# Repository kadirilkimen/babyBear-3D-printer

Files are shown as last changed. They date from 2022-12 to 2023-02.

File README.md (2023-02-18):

# the babyBear 3D Printer
## A very small 3D printer! that slightly smaller than an A4 paper including a spool of filament.

Just the footprint is small. It has a 160mm diameter build plate and up to 300mm work height.
It's a complete 3D printer with quick change tool head. So the plan is making it a laser cutter and cnc milling machine along with printing.

```diff
+ All STL and BOM files have been updated.

! See the assembly animations on this link : https://kadirilkimen.com/babybear/assemblyanimations/
! Note that the animations are not final and not covers all the machine yet.
```
# Marlin now has Polar kinematics!
Finally, I developed polar kinematics and the Marlin team merged it to the main distribution.
That means you can just slice the model and send to the babyBear without post processing.

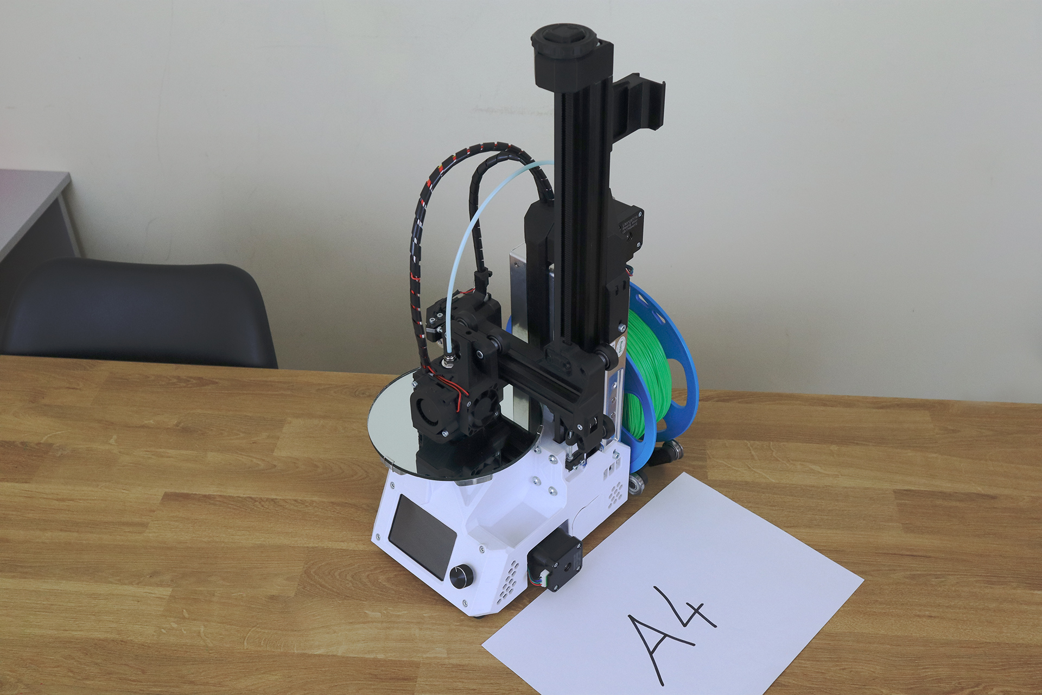
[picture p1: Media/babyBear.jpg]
babyBear Optional title


## Great people who helped me on this project.

Most of the babyBear components donated by V-slot Poland.

Filaments and some local logistics provided by RE3D filaments.

If you are located in Europe, I recommend you to visit their website.

https://vslot-poland.com/en_US/index

https://re3d.eu/

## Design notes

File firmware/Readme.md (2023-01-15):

# Intro
If you don't know how to work with firmware, jump to the **shortcut** section.
**babyBear_firmware.bin is a compiled Marlin to work with recommended controller board, display and drivers.**

### babyBear developed around and tested with Marlin firmware
It is possible to use a different firmware.
I just decided not to split my energy on a lot of options.
If you can make other firmware work with the babyBear, feel free to perform a pull request.

## shortcut
If you have the firmware file, it is very simple.
- download the firmware file [babyBear_firmware.bin](babyBear_firmware.bin).
- Put the firmware file into an SD card.
- Insert SD card into the machine.
- Turn on the machine.
- You would see messages like "erasing" or "uploading".
- Once it is done, you will see Marlin printer interface.
- Done! Happy printing!

## Basics
### If you don't need any customization and you have the recommended hardware
- Just follow the **shortcut** section.

### If you have different hardware or want to do some customizations with Marlin firmware
- Follow **How to install Marlin** and **How to configure Marlin**

### Ah, you are the rogue one?
- Well, at least take a look at configuration files here.

## How to install Marlin
Polar kinematics added to Marlin by bugfix.2.1.x

babyBear doesn't require any special step.
Please follow official Marlin guide:
https://marlinfw.org/docs/basics/install.html

Just like each machine, you must edit configuration.h and configuration_adv.h files
- If you are using the recommended hardware, you can use the [Configuration.h](Configuration.h) and [Configuration_adv.h](Configuration_adv.h) files.
- for other hardware, follow the **Configuration** section

## How to configure Marlin
- uncomment #define POLAR line.
- To have a starting point, copy the step, feedrate and acceleration settings from [Configuration.h](Configuration.h)
- uncomment #define LIN_ADVANCE line in the Configuration_adv.h file.
- Set ADVANCE_K to 0.15, or perform a calibration test to find out the best one. However,  polar axis motions near the center is weird and requires a lot of work. You would just save your time and go with 0.15 :)
- If you don't have the recommended hardware, perform the hardware related configurations. 

## Recommended and tested hardware
- MKS Robin nano v3 Board.
- TMC 2209 drivers
- MKS TS35 display.
- BMG type extruder with 3:1 reduction.

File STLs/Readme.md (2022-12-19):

# Read this before start printing

### Material
Original prototype printed with PETG filament.
Because it is an overall best compromise for;
- heat resistance,
- printability,
- dimensional stability,
- strength.

If you choose a different material, please keep in mind that electronics, motors and power supply creates significant heat.

### Part orientation
All parts are oriented according to required strength and printability.
I recommend printing all parts in their original orientation.

### Nozzle and layer height
Printable parts are designed to print with 0.4mm nozzle and 0.2mm layer height.
If you prefer less layer height, prefer 0.1mm. Other layer heights may cause some detail to be lost.

### Printing precise parts
Almost everything about FDM printing is relative and it is not simple to print precise parts.

#### Understanding temperature effects
Printing at a correct temperature is critical to achieve precision in FDM parts.
Filament manufacturers have their own material blends. Therefore, a very best temperature value for a filament wouldn't be the best for another brand.
The manufacturers mostly recommend best temperature range for their filaments.
Usually, printing at lower end of this range gives better surface quality, which is very important for precision.
However, lower temps. also reduces the fusing between layers and part becomes weaker.
So you would prefer to find best compromise spot between the surface quality and the strength.

#### Printer's positioning accuracy
Especially the 3D printers come as kits, mostly don't have a good positioning accuracy.
You would expect 0.1mm deviation on dimensions.
Parts of the babyBear designed to have 0.2mm tolerance to each other and off the shelf components.
Make sure your printer's positioning accuracy is better than 0.1mm.
If it is not, then calibrate your printer's hardware and stepper motors.

#### Squareness of the printer
Very less 3D printer model comes with a good square frame.
If your printer came as kit and you assembled it yourself, it is probably not square at all.
If you are into printing precision parts, I recommend you to get machinist right angle squares.

Using right angle, check all the linear rails and adjust them until they are square each other.
To get more information about squaring, it is called Tramming in machine industry. Check youtube for cnc machine/3d printer tramming.

Let's say if your printer is not square enough;
In this case Z axis wouldn't be parallel to the rotary axis of the babyBear. This means, in higher Z distances, your part will become narrower or wider.
Rotary axis rotor won't be cylinder enough and it will wobble. This wobble will be amplified by Z height.

So the squareness of your printer is very important.

#### Dimensional accuracy of the parts.
To make sure the 3D printed parts in a good tolerance, first print some test parts and try if they fit properly.

For example, I printed a section of rotary axis rotor to check 16010 bearing ID tolerance and again printed a section of the main body to check 16010 bearing OD tolerance.

Especially the bearings must fit to the place with a little tightness. If it is too tight, it will deform the printed body while mounting. If it is loose, it won't create precise movement under load.

On the bearing mounting surfaces, only use sanding to remove imperfections. If the surface is not accurate enough, then I recommend to print the part from scratch.

### Post processing
Even under best circumstances, 3D printed parts still can have problems.
FDM printers tend to smooth inside corners and make bulgy ends on outside corners.
So you have to sand down these imperfections, if necessary.

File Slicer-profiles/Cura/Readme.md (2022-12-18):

# Cura machine profile for the babyBear

## Instructions
- Go to the Cura configuration folder. You can find it in Cura main menu : Help > Show configuration folder.
- Make sure that there is no running Cura.
- Copy the "definition_changes", "machine_instances" and "user" folders into the configuration folder. Overwrite the folders.
- Next time you open Cura, you will see "the babyBear" next to your other printer profiles.

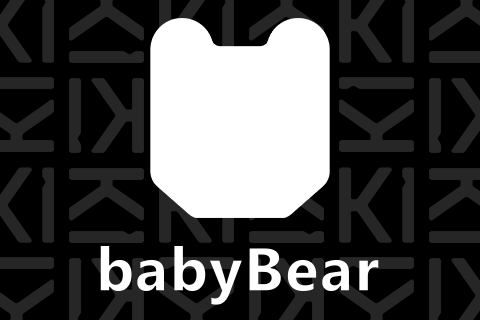
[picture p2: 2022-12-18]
Media/babyBear-bootscreen.png

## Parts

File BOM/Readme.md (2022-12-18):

## **ODS is a spreadsheet file format. Any office software can open it.**
### If you don't have office software, you can give Libreoffice a shot  https://www.libreoffice.org/

## **Components**
Component links are carefully selected. But I didn't buy them directly.
Most of the babyBear components donated by V-slot Poland.
The rest were collected from local stores.

I bought average quality 16010 bearings from a local store for 4USD each and F608 bearings from aliexpress for less than 1USD each.
I don't recommend cheapest bearings. They tend to be very bad. But best selling cheap bearings are usually good enough for such projects.

## **Consumables**
Consumable items you will need while building the babyBear.

## **Fasteners**
Online stores often sell fasteners in odd varieties and quantities.
It would be easier to get fasteners from a local shop.

There are different fastener grades. Usually you can see 8.8, 10.9, 12.9 etc.
Higher the number means stronger the fastener.
I recommend fasteners grade higher than 8.8 for this project.

## **Tools**
You probably will need those tools to build the babyBear.
They are also common tools for 3D printing and such projects.

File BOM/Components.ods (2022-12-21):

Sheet: Sheet1
Electronics
Type | Size | Quantity | Description | Amazon

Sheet: Sheet2
Electronics
Type | Size | Quantity | Description | Amazon
MKS Robin nano v3 controller +TS35 display + TMC2209 drivers | - | 1 | I recommend to buy them as a kit. | https://amzn.to/3um2EEK
24V – 350W Slim type Power supply. Dimensions are important! | W:115mm L:215mm H:30mm | 1 | Please keep in mind. Power quality affects overall electronics. I strictly recommend to use a good quality product | https://amzn.to/3h1wlbl
Stepper motor | Nema 17 | 4 | Min. 40mm length recommended. Connectors SH-2.54 | https://amzn.to/3VwYYfk
Snap fit – Power inlet (See reference photo. Any different power inlet won’t fit ) | - | 1 | Already wired one recommended to avoid working on AC current. | https://amzn.to/3HbvpvO
Limit switch (See reference photo) | 20mm | 2 | Any standard 3 pin microswitch would work. | https://amzn.to/3VwhR2a
Fan 24V | 40x40x10 | 2 | If available, Prefer ball bearing ones. One with long and one with short cable needed. | https://amzn.to/3XZXI67
Blower fan 24V | 40x40x20 | 1 | If available, Prefer one with ball bearing and long cable | https://amzn.to/3FnKsB0
Heat shrink tubes | ~ | 1 |  | https://amzn.to/3P1mpv1
Wiring
Type | Size | Quantity | Description | Amazon
Min. 1.5mm2(16AWG) blue cable | 25cm | 1 | Power inlet to PSU (unnecessary, if you buy power inlet with wiring)
Min. 1.5mm2(16AWG) brown cable | 25cm | 1 | Power inlet to PSU (unnecessary, if you buy power inlet with wiring)
Min. 1.5mm2(16AWG) yellow-green cable | 25cm | 1 | Power inlet to PSU (unnecessary, if you buy power inlet with wiring)
Min. 1.5mm2(16AWG) red cable | 25cm | 1 | PSU to controller board
Min. 1.5mm2(16AWG) black cable | 25cm | 1 | PSU to controller board
Min. 1.5mm2(16AWG) Cable terminals for Power inlet | - | 5 | Power inlet to PSU (unnecessary, if you buy power inlet with wiring)
Min. 1.5mm2(16AWG) Cable terminals for PSU | - | 5
Min. 1.5mm2(16AWG) Cable lugs for Controller Power inlet | - | 2
2 core 22awg cable for fans and switches | 300cm | 1
Cable wrap | 200cm | 1
AC power cable fits to power inlet | ~ | 1
Bearings
Type | Size | Quantity | Description | Amazon
16010 Bearing | ZZ or RS | 2 | 50x80x10mm | https://amzn.to/3FpQhhg
F608 flanged bearing | ZZ or RS | 6 | 8x22x7mm ( flange diameter : 25mm ) | https://amzn.to/3H9jLkQ
OpenBuilds
Type | Size | Quantity | Description | Openbuilds | Amazon
20x40mm v-slot extrusion | 250 to 500mm | 1 | 400mm used in the prototype. 500mm is a little extreme for this machine. | https://openbuildspartstore.com/v-slot-20x40-linear-rail/?ref=pIsLSjOaWeoY4 | https://amzn.to/3P28tAR
20x20mm v-slot extrusion | 150mm | 1 | There is only exact 150mm space for the 20x20 extrusion. | https://openbuildspartstore.com/v-slot-20x20-linear-rail/?ref=pIsLSjOaWeoY4 | https://amzn.to/3F0TKSb
Openbuilds V-slot wheel | Normal size | 6 |  | https://openbuildspartstore.com/solid-v-wheel-kit/?ref=pIsLSjOaWeoY4 | https://amzn.to/3F4LJLY
Openbuilds spacer | 6mm | 4 | Eccentrics and spacers must have exact same height | https://openbuildspartstore.com/aluminum-spacers-10-pack/?ref=pIsLSjOaWeoY4 | https://amzn.to/3VvlDZL
Openbuilds eccentric nut | 6mm | 2 |  | https://openbuildspartstore.com/eccentric-spacer/?ref=pIsLSjOaWeoY4
Rubber Feet | M4 or M5 | 4 | I used one from a local store. OD:14mm, H:10mm, Screw size is M4 and screw length after rubber is : 6mm | https://openbuildspartstore.com/rubber-feet-set-4-pack/?ref=pIsLSjOaWeoY4 | https://amzn.to/3Y7iReW
Low profile Tee Nuts for rubber feet | M4 or M5 | 4 | Must match rubber feet | https://openbuildspartstore.com/tee-nuts-m5-10-pack/?ref=pIsLSjOaWeoY4 | https://amzn.to/3Haw2FN
Belt drive
Type | Size | Quantity | Description | Openbuilds | Amazon
6mm GT2 pulley | 16T, 5mm hole | 3 | For X, Y, Z motors |  | https://amzn.to/3upyl06
6mm GT2 idler pulley | 16T, 3mm hole | 1 | X belt idler pulley, 3mm inner hole with bearings |  | https://amzn.to/3HdWSwG
6mm GT2 idler pulley | 20T, 5mm hole | 1 | Z belt idler pulley, 5mm inner hole with bearings |  | https://amzn.to/3upypwS
6mm GT2 open belt | 2000mm | 1 | For X and Z drive | https://openbuildspartstore.com/gt2-2m-timing-belt-by-the-foot/?ref=pIsLSjOaWeoY4 | https://amzn.to/3VILLjC
6mm GT2 closed loop belt | 300mm | 1 | For Rotary axis drive |  | https://amzn.to/3F2gUaN
6mm GT2 closed loop belt | 200mm | 1 | For Z axis reduction drive
Extruder
Type | Size | Quantity | Description | Amazon.com
Bowden extruder (right hand if applicable) | - | 1 | Any good bowden extruder of your choice | https://amzn.to/3Vj7Rbs
Bowden tube | 50cm | 1 | ID:2mm, OD:4mm | https://amzn.to/3FF3DoM
E3D V6 – 24V compatible hotend assembly | - | 1 |  | https://amzn.to/3upQ9rQ
Printbed supplies
Type | Size | Quantity | Description | Amazon
Glass bed clips (see reference photo) |  | 6 | Due to the very tight space around the work bed, only very specific clips would work. | https://amzn.to/3izk3ax
Externally supplied parts
Type | Size | Quantity | Description | Source
Acrylic worktable substrate ( If you don’t print one ) | 5 to 6mm thickness | 1 | Mounting surface of the working surface. I preferred a laser cut acrylic sheet. | Local laser cut shop
Glass/mirror or polycarbonate printing bed, 160mm diameter | max 4mm thickness | 1 | For glass, 3 or 4mm acceptable. If you can find 3mm glass, it is great because it is lighter. For polycarbonate, go for 4mm | Local shop

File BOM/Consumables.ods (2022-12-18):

Filaments for building the machine
Size | Description | EU Source | US Source
PETG filament (White parts on the prototype) ~1kg | RE3D is my local filament supplier. They produce their own filaments and they are very good. If you are in Europe, consider buying from them. | https://re3d.eu/product-category/filament/petg/?wmc-currency=EUR | https://openbuildspartstore.com/petg-3d-printer-filament/?ref=pIsLSjOaWeoY4
PETG filament (Black parts on the prototype) ~1kg
Other consumables
Size | Description | Recommended Source | US Source
Super glue | We need to glue a few parts and some nuts to the place | https://amzn.to/3h1pOgI
Cable ties | To organize cables and fix cable wraps to the printer. | https://amzn.to/3Hfj0a8
Aluminium heat insulation tape | To insulate hotend body from heat radiation | https://amzn.to/3OYAF7C
Glue for the printbed | Because we don’t have a heated bed yet, we need the glue to stick the part to the printbed

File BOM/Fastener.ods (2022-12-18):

Socket bolt - DIN 912
Size | Quantity | Amazon
M3x10 | 26 | https://amzn.to/3uo4Ont
M3x12 | 11
M3x16 | 4
M3x20 | 11
M3x30 | 4
Countersunk bolt – DIN 7991
Size | Quantity | Amazon
M3x16 | 3 | https://amzn.to/3B9y6Kv
M5x10 | 2 | https://amzn.to/3HbvkIs
Low profile hex socket bolt
Size | Quantity | Amazon | Openbuilds
M5x20 | 4 | https://amzn.to/3Wn13uw | https://openbuildspartstore.com/low-profile-screws-m5-10-pack/?ref=pIsLSjOaWeoY4
M5x30 | 8 |  | https://openbuildspartstore.com/low-profile-screws-m5-10-pack/?ref=pIsLSjOaWeoY4
Button head bolt - ISO 7380
Size | Quantity | Amazon
M4x10 | 3 | https://amzn.to/3VSeCBT
M5x10 | 4 | https://amzn.to/3VQarXd
M5x16 | 4
M5x40 | 5 | https://amzn.to/3P2A05p
M5x60 | 2
Hex Nut - DIN 934
Size | Quantity | Amazon
M3 | 47 | https://amzn.to/3FY102W
M5 | 1
Nylon lock nut – DIN 985
Size | Quantity | Amazon | Openbuilds
M5 | 7 | https://amzn.to/3F0inyk | https://openbuildspartstore.com/nylon-insert-hex-locknut-m5-10-pack/?ref=pIsLSjOaWeoY4
Drop-in T Nut for V-slot extrusions
Size | Quantity | Amazon | Openbuilds
M5 | 17 | https://amzn.to/3HarEXw | https://openbuildspartstore.com/nylon-insert-hex-locknut-m5-10-pack/?ref=pIsLSjOaWeoY4
Washer – DIN 125
Size | Quantity | Amazon
M4 (9x~4x0.8) | 1 | https://amzn.to/3VADv5m
M5(10x~5x1) | 15

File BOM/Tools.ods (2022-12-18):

Machines and electronics
Type | Size | Quantity | Amazon | Description
3D printer | min print area 220x210 required | 1 | https://amzn.to/3BLBdZb | I don’t have a prusa. My first printer was Twotrees bluer (seems discontinued). Now I build my own printers and wouldn’t buy any cheap printer.
Digital Multimeter |  | 1 | https://amzn.to/3h8zNAU | Auto-range multimeters are very easy to use
Digital Caliper |  | 1 | https://amzn.to/3G1HTFh | Always prefer good quality measuring tool
Basic Tools
Type | Size | Quantity | Amazon
Wrench | 6mm | 1 | https://amzn.to/3Ux7x8S
Wrench | 8mm | 1
Wrench | 10mm | 1
Threading Tap | M3 | 1 | https://amzn.to/3ukEIBX
Threading Tap | M5 | 1
Hex key set |  | 1 | https://amzn.to/3VyezeT
Wire Cut, strip, Crimp tool |  | 1 | https://amzn.to/3HbPr9u
Soldering equipment |  | 1 | https://amzn.to/3ULjwQp
Drill bit | 2mm | 1 | https://amzn.to/3H8bDkE
Drill bit | 3mm | 1
Drill bit | 5mm | 1
Countersink drill |  | 1 | https://amzn.to/3B9eaXY
Deburring Tool |  | 1 | https://amzn.to/3Vuk65X
Sandpapers
Needle file set |  |  | https://amzn.to/3XWLN9d
Cable tie gun |  | 1 | https://amzn.to/3UxwGjy
Utility knife |  | 1 | https://amzn.to/3XQTMVr
Machinist right angle square |  | 1 | https://amzn.to/3VwoDVK | Always prefer good quality measuring tool

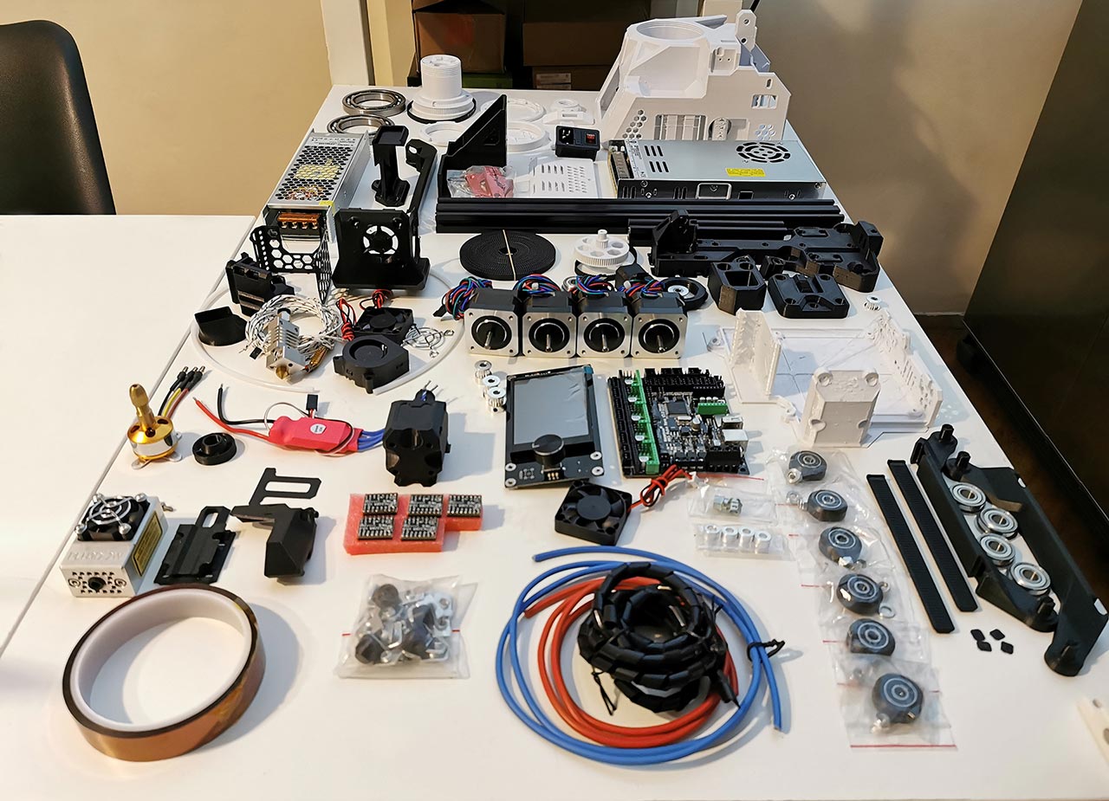
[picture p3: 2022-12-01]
Media/parts.jpg

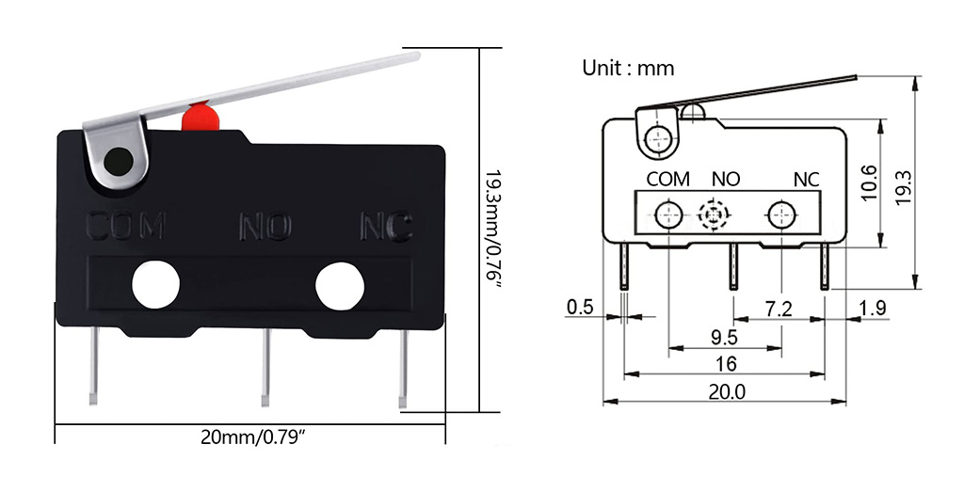
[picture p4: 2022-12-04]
BOM/reference-images/limit-switch.jpg

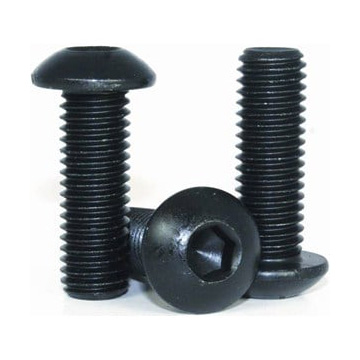
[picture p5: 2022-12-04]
BOM/reference-images/button-head-bolt.jpg

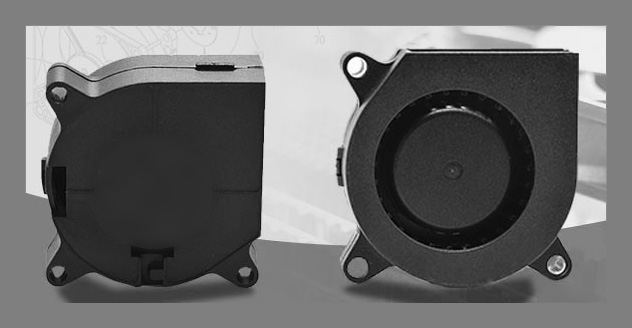
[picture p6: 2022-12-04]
BOM/reference-images/blower-fan.jpg

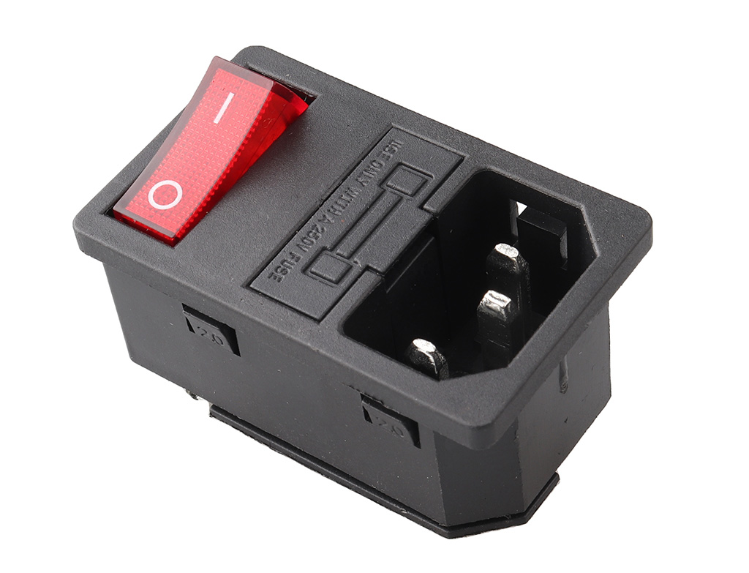
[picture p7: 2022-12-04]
BOM/reference-images/power-inlet.jpg

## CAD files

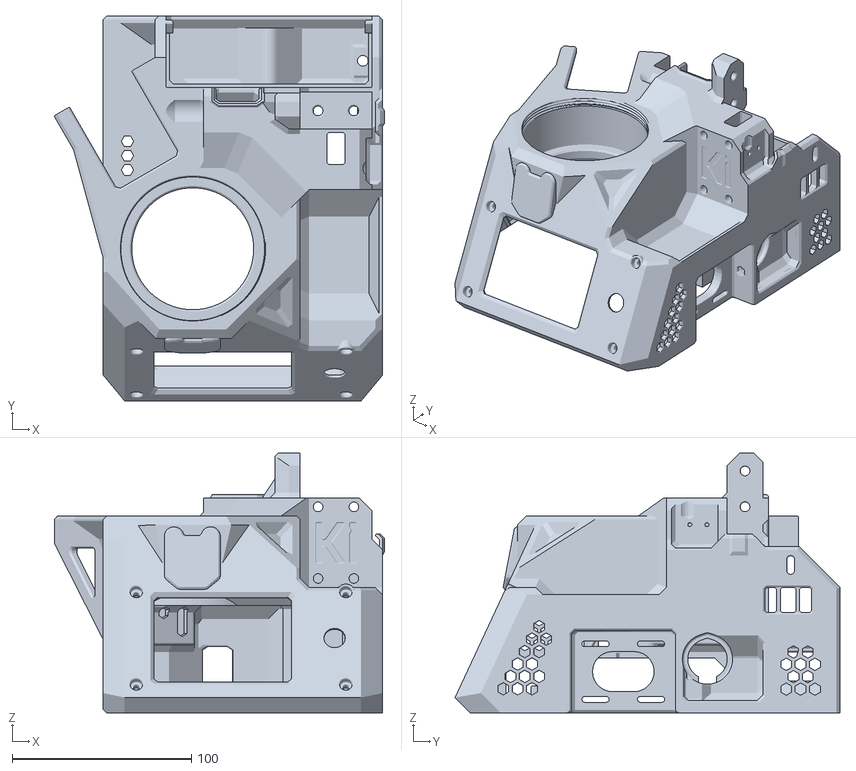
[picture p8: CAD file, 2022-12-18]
STLs/Without-supports/Main-body.stl
184.3 x 215.0 x 145.0

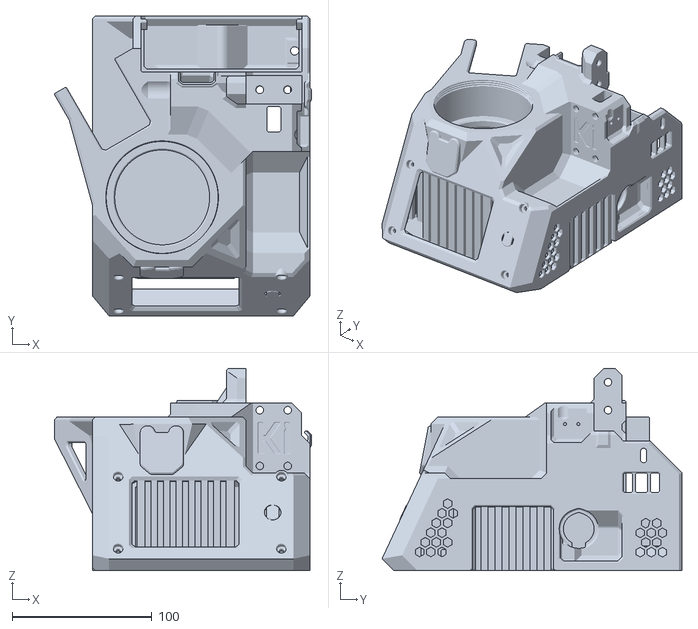
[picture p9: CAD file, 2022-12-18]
STLs/Built-in-supports/Main-body.stl
184.3 x 215.0 x 145.0

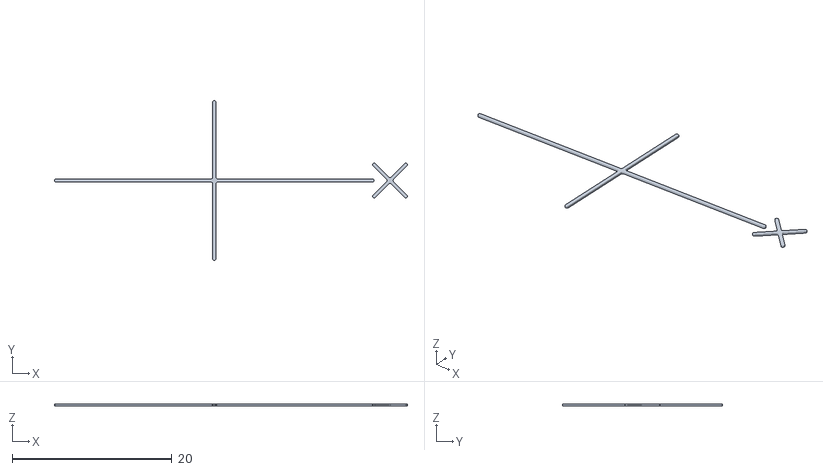
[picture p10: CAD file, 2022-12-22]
Docs/Calibration/Hotend-calibration-lines.stl
44.2 x 20.0 x 0.25

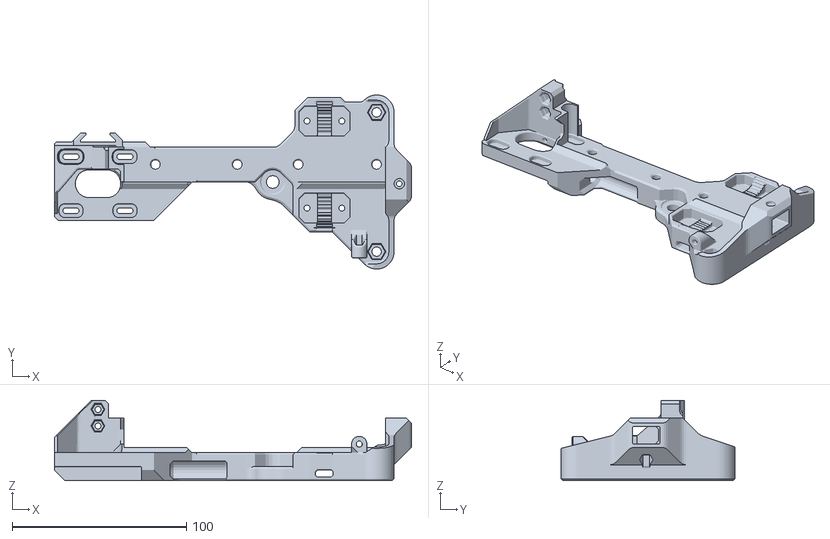
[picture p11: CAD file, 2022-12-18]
STLs/Built-in-supports/Z-axis-carriage.stl
205.0 x 100.0 x 46.0

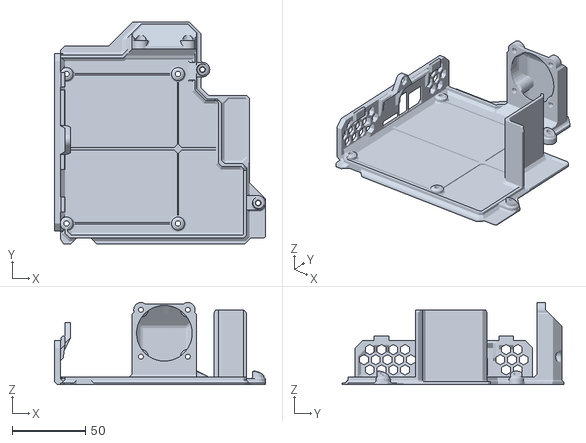
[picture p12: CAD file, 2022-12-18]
STLs/Without-supports/Bottom-cover.stl
144.0 x 151.5 x 56.0

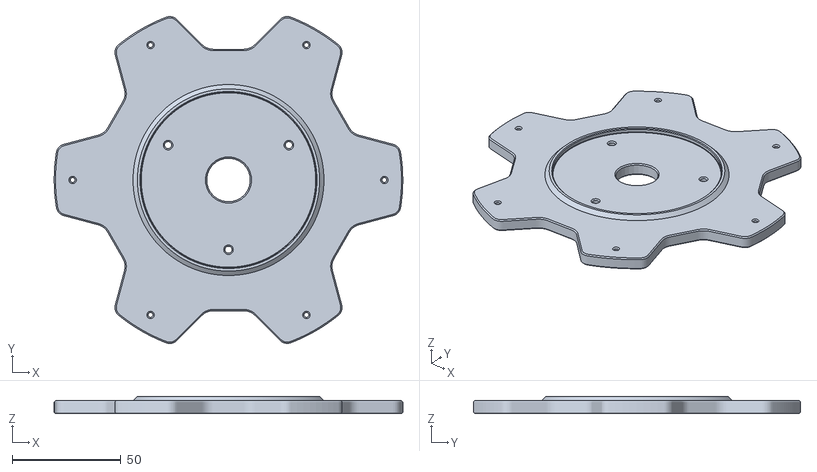
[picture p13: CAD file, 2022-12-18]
STLs/workplate/for-3D-print/work-place-substrate-PETG-recommended.stl
160.0 x 150.1 x 8.00

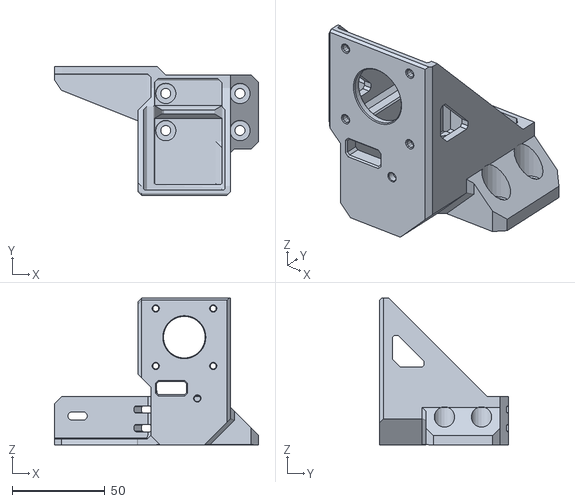
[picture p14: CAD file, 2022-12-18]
STLs/Built-in-supports/Extruder-body.stl
110.0 x 69.5 x 79.0

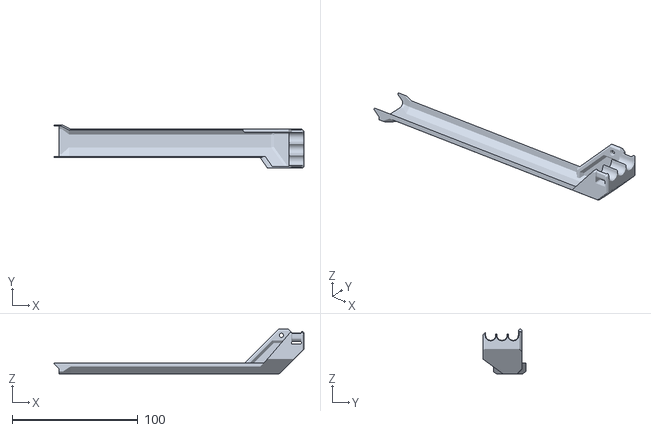
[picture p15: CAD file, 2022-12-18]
STLs/Built-in-supports/Cable-channel.stl
199.0 x 34.0 x 35.8

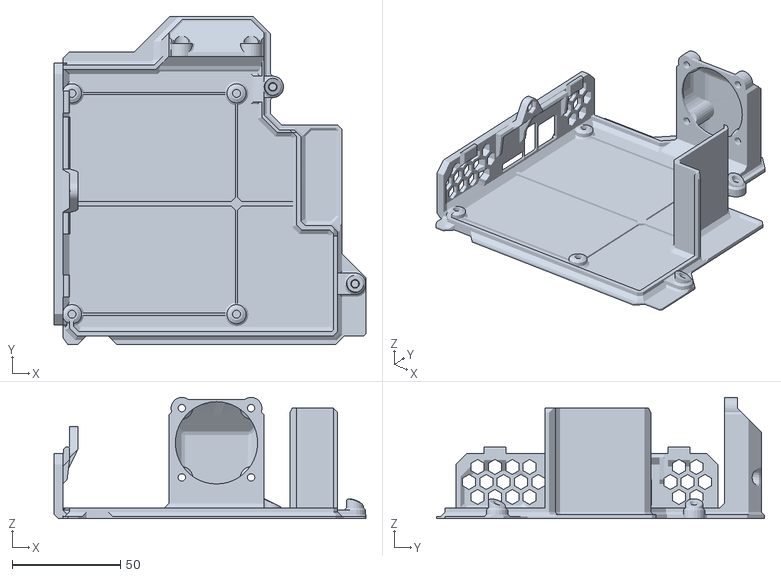
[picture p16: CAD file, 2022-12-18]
STLs/Built-in-supports/Bottom-cover.stl
144.0 x 151.5 x 56.0

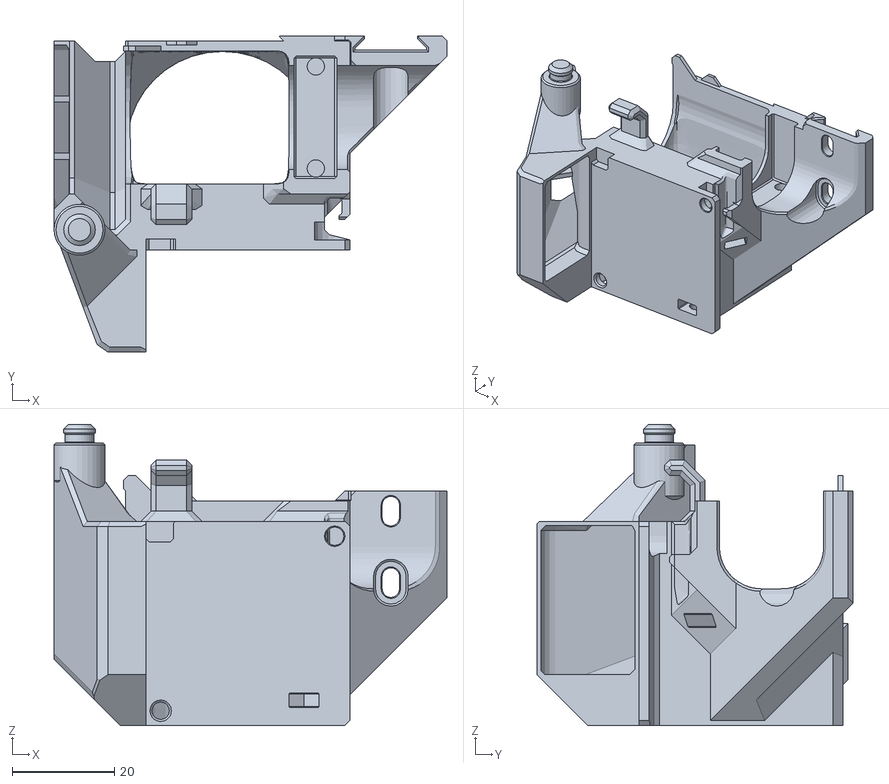
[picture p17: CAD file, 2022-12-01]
STLs/Built-in-supports/Hotend-body.stl
77.0 x 62.0 x 59.0

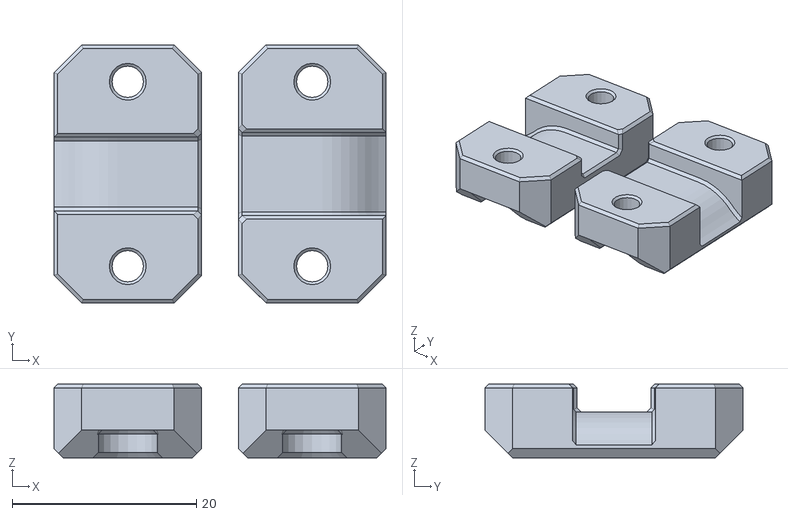
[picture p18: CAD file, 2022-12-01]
STLs/Without-supports/Z-axis-belt-clamps.stl
36.0 x 28.0 x 8.00

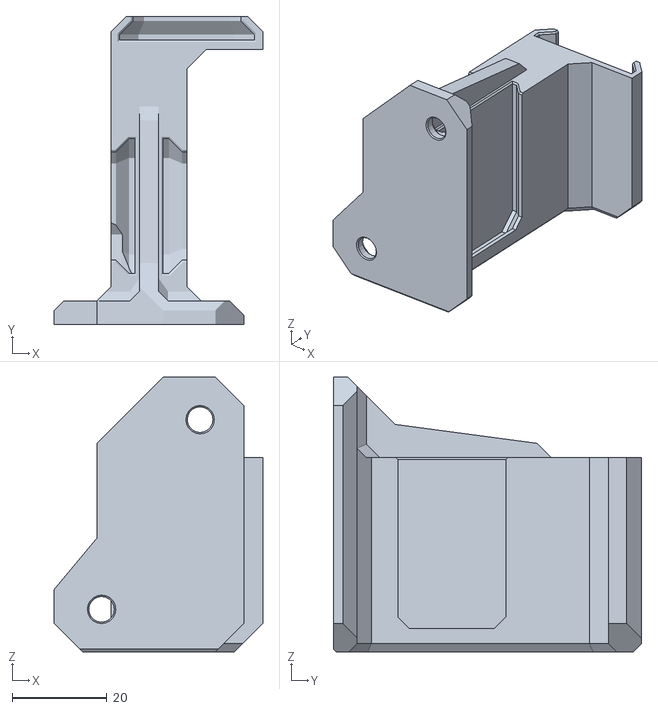
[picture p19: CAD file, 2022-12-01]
STLs/Built-in-supports/Tool-holder.stl
44.0 x 65.0 x 58.0

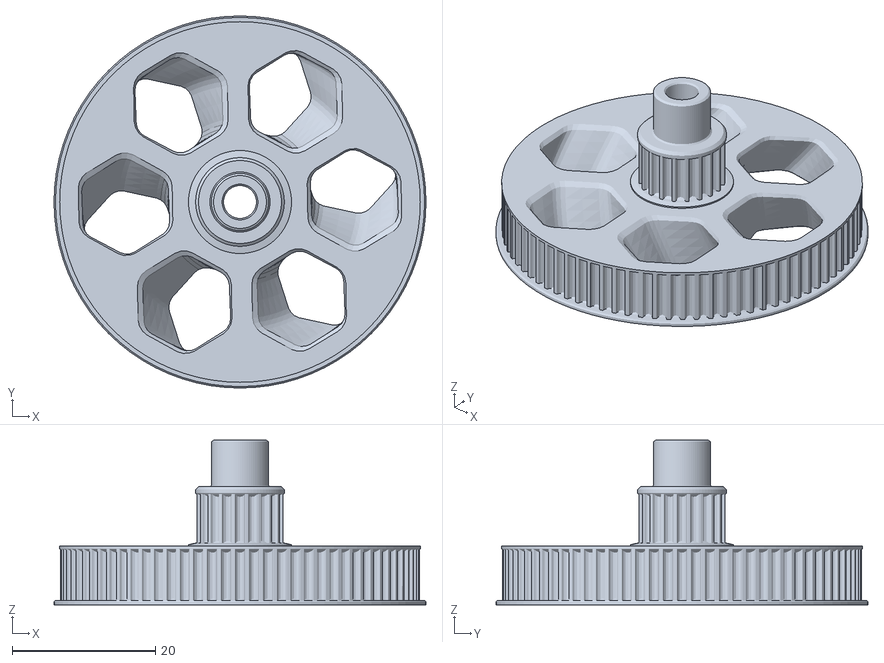
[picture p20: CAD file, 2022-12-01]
STLs/Without-supports/Z-drive-pulley.stl
52.0 x 52.0 x 23.0

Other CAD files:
STLs/workplate/for-laser-cut/acrylic-workbed-surface-acrylic(pmma)-6mm.dwg
STLs/workplate/work-bed-glass-or-polycarbonate-max-4mm.dwg
STLs/Built-in-supports/Bearing-cover.stl
STLs/Built-in-supports/Hotend-clamps.stl
STLs/Built-in-supports/Hotend-grill.stl
STLs/Built-in-supports/Hotend-tool-socket.stl
STLs/Built-in-supports/PSU-cover.stl
STLs/Built-in-supports/Rotary-axis-bearing-lock-nut.stl
STLs/Built-in-supports/Rotary-axis-bearing-spacer.stl
STLs/Built-in-supports/Rotary-axis-motor-mount-nut.stl
STLs/Built-in-supports/Rotary-axis-motor-mount-washer.stl
STLs/Built-in-supports/Rotary-axis-motor-mount.stl
STLs/Built-in-supports/Rotary-axis-preload-nut.stl
STLs/Built-in-supports/Rotary-axis-rotor.stl
STLs/Built-in-supports/Rotary-axis-tool.stl
STLs/Built-in-supports/Spool-pins.stl
STLs/Built-in-supports/Spool-support-spacer.stl
STLs/Built-in-supports/Spool-supports.stl
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

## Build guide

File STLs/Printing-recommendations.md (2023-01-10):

# Recommended print settings for the parts

## for all the parts

### 0.4mm nozzle is the most common one. Therefore 0.4mm nozzle size affected any nozzle size related dimensions. It is recommended to use 0.4mm nozzle. But also 0.6mm  would work too.

### Speed is enemy of precision and accuracy on a 3D printer. Most of the prototype printed around 50mm/s feedrate. If you want to shorten printing time, you would prefer to speed up inside lines and keep the outer wall and skin slow.

### To get a better final surfaces for rotary axis bearing mount, I recommend to activate ironing.

### The values about the Strength/Surface are for reference to stress what is more important for the part. Because the printer you have, speed and filament all relative, You would use this value and your experience to figure out best speed and nozzle temp, cooling etc. Please note that, higher the surface quality means better precision.
- 100% : The strength of the part is the most important and we don't need much surface quality/precision at all.
- 50% : Both strength and surface quality are important. We can't get them both ( if you are a crazy pro super skilled 3D printer person, hats off ). Therefore we sacfrifice from both to get best compromise.
- 0% : The strength is not so important and we would prefer to get best surface quality.

### 100% solid parts means it is completely solid. Some people do this by 100% infill. Some people prefer to fill the part all with the wall.In my opinion, filling the part with wall is best for most cases. But sometimes, infill lines may bring more strength because of the line directions. Inspect the part and decide yourself.

## ---------------------------------------------------
## For all printable parts
- Layer height : 0.2mm
- Line width : 0.4mm
- Wall count : min. 2
- Infill line width : 0.6mm
- Infill density : min. 10% 
- Infill type : Cubic subdivision
- Print speed : under 100mm/s
- Strength/surface : 40%

## ---------------------------------------------------
## 100% solid parts
- Strength/surface: 50%
#### ------------------------
- Hotend-clamps.stl
- Hotend-grill.stl
- Hotend-tool-socket.stl
- Tool-nut.stl
- Z-axis-belt-clamps.stl

## ---------------------------------------------------

##  Z Drive Pulley
### It is difficult to print GT2 pulley teeth with 0.4mm nozzle but not impossible. 0.2mm is best radius you can get with 0.4mm nozzle it creates more smooth teeth profile than actual GT2 profile. The settings below helps to get better GT2 profile. I printed the prototype with 0.4mm and so far works fine. If you have a chance, I recommend to print with a smaller nozzle.
- 100% solid
- Layer height: 0.1mm
- Line width : 0.4mm or less
- Strength/surface : 50%
- Print speed : 75mm/s or less
#### ------------------------
- Z-drive-pulley-pin.stl
- Z-drive-pulley.stl

## ---------------------------------------------------
## Structural parts
### Printing parts with threads requires extra attention. I recommend to print 3D printed nuts a little under-flow. It helps preventing over-tight threads.
### Consider printing following parts a little underflow : Rotary-axis-bearing-lock-nut.stl, Rotary-axis-preload-nut.stl, Z-axis-belt-tensioner-nut.stl
- Wall count : min. 3
- Infill density: min. 15%
- Strength/surface: 50%
#### ------------------------
- Extruder-body.stl
- Hotend-body.stl
- Main-body.stl
- Rotary-axis-bearing-lock-nut.stl
- Rotary-axis-bearing-spacer.stl
- Rotary-axis-motor-mount-nut.stl
- Rotary-axis-motor-mount-washer.stl
- Rotary-axis-motor-mount.stl
- Rotary-axis-preload-nut.stl
- Rotary-axis-rotor.stl
- Rotary-axis-tool.stl ( PLA recommended )
- Spool-supports.stl
- Tool-holder.stl
- X-axis-belt-clamps.stl
- X-axis-carriage.stl
- Z-axis-belt-tensioner-nut
- Z-axis-carriage.stl
- Z-drive-tensioner.stl
- Z-drive-top-support.stl

## ---------------------------------------------------
## Lightweight parts
- Strength/surface : 25%
#### ------------------------
- Bearing-cover.stl
- Bottom-cover.stl
- Cable-channel.stl
- PSU-cover.stl
- Spool-pins.stl
- Spool-support-spacer.stl
- X-axis-cable-mount.stl

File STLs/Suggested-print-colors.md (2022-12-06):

## Original prototype printed in the colors below. Feel free to choose your own colors

### **Color: Black, Material: PETG**
- Cable-channel
- Extruder-body
- Hotend-body
- Hotend-clamps
- Hotend-grill
- Hotend-tool-socket
- Spool support-spacer
- Spool-supports
- Tool-holder
- X-axis-belt-clamps
- X-axis-cable-mount
- X-axis-carriage
- Z-axis-belt-clamps
- Z-axis-belt-tensioner-nut
- Z-axis-carriage
- Z-drive-tensioner
- Z-drive-top-support

### **Color: White, Material: PETG**
- Bearing-cover
- Bottom-cover
- Main-body
- PSU-cover
- Rotary-axis-motor-mount-nut
- Rotary-axis-motor-mount-washer
- Rotary-axis-motor-mount
- Rotary-axis-bearing-lock-nut
- Rotary-axis-rotor

### **Color: Doesn't matter, Material: PETG**
- Rotary-axis-bearing-spacer
- Rotary-axis-preload-nut
- Spool-pins
- Tool-nut
- Z-drive-pulley-pin
- Z-drive-pulley

### **Color: Doesn't matter, Material: PLA**
- Rotary-axis-tool

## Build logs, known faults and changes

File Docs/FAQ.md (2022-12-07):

# **Frequently asked questions about the babyBear and polar printers**

## Is the babyBear just a smaller version of the PolarBear?
No. the Polar bear is a flexible machine. You can use any controller board, software or firmware to give it a custom purpose.
On the other hand, the babyBear is a 3D printer with ability to add milling spindle and laser cutter.

## **How much does it cost to build?**
It would cost somewhere around 200 to 400 USD.
It depends on your purchasing decisions and market situation.
Please keep in mind, some small items like nuts and bolts mostly come in packs not the exact amount if the 

## **Does the babyBear have a heated bed?**
Unfortunately, current version doesn't have a heated bed.
I have been successful to transfer power to the infinitely rotatable printing bed.
However, reading back the temperature is a big issue. Both standard 3D printer electronics and software is not suitable for this purpose.
I am working on a marlin update and an electronic solution.

## **What skills do I need to build the babybear?**
3D printing experience with PETG(or similar material of your choice).
Good experience with electrical connections.
Basic understanding of electronic circuits.
Basic mechanical assembly skills and experience with the required tools.
You may need to perform some soldering.

## **Could the babyBear be my only 3D printer?**
Of course it can. However, I recommend you to have a regular printer too.
Software and most hardware doesn't have a good support for polar 3D printers yet. You have to tinker around to make it work.
It would be good to have a regular 3D printer that works without tinkering.

## **Is it good to start 3D printing with the babyBear?**
I wouldn't recommend polar printers as first printer. It is better to gain some experience on a standard 3D printer.

## **Why a polar machine is better than a cartesian one?**
Comparing such different systems is not the best way to judge a polar machine.
The babyBear can perform everything you can do on a cartesian 3D printer.
Cartesian 3D printers can follow straight lines better and polar 3D printers can follow curves better.
If you are not going to print just cubes, you will end up models with both curves and straight edges.
Depending on what shapes you have more on the part, one will outperform the other in terms of surface quality.
On the other hand, a polar axis can perform some tasks that a cartesian printer can't. You have a possibility to approach workpice from sides.
This gives you opportunity of performing tasks like sculpting, pottery, 4Dish milling/printing etc. Of course you need software or creative ways to perform those tasks. Yet, even with software and creative tasks, a cartesian machine can't offer those opportunities.
Cartesian machines outperform polar machines in terms of simplicity and being off the shelf. All software and hardware are already tuned for them.
A polar printer has a great advantage in vase(surface) mode printing(single wall shell printing). It can create much better surface in vase mode and can print faster.

## **What is the advantage of a polar printer in vase mode printing?**
In vase mode, a printer creates single wall shell. This allows the printer to go only one direction without interrupting the extruding process.
However, a cartesian machine has to change directions in X and Y axis constantly to perform vase mode operations. This requires slow downs and speed ups in X an Y direction changes. Even if you set good printing speed, those speed changes reduce overal speed and create possibility of inaccuracies. Extrusion process is not a fast process. It can't keep up with constant speed changes. Therefore you end up having more material in some places and less material in other places instead of a constant volume of material.

In a polar printer, rotary axis can spin in one direction indefinitely. Unless the part has a complex geometry, it doesn't have to spin back. Therefore speed downs and speed ups are a lot less than a cartesian one. This helps keeping up with the expected speeds and reduces extrusion inaccuracies. Therefore creates more constant material volume and better surface quality.

## **Why the rotary axis bearings are so big?**
Bigger bearings help to distribute forces to a larger area of the printed parts.
Because 3D printed plastics are not as rigid as metals, too much force in a small area cause deformations.
If we use small bearings, all the force applied on work bed would be focused on a small area on the printed parts.

## **Can I build and sell the babyBear?**
Please check the project license and get legal advice.

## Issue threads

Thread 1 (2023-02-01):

Turntable acceleration and deceleration problem

Melkiyby, 2023-02-01:
Hi! I am using your project. But I got a small bug. When the motion trajectory passes through the center of the turntable and it needs to turn 180 degrees, the rotation starts with a smooth acceleration, but when it reaches 180 degrees, the table stops without slowing down and the motor can jump a few steps.
Could you help find a solution to this problem?
https://youtube.com/shorts/HvbnYGIs35s?feature=share
And one more bug related to the z-axis. After some time, it stops rising for crossings and works only down.
It's definitely not a mechanical problem. On the firmware from Rob Mink [(URL)](https://github.com/RobMink/UpdatedPolarFirmware---Marlin) it worked more stable, but also not perfect. On a complex engraving with many ups and downs, the result is about the same.

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

kadirilkimen, 2023-02-01:
In January, I developed polar kinematics for Marlin and the Marlin team merged it into the firmware.
If you use this old cartesian system firmware, I strongly suggest to move on to the Marlin with polar kinematics.
Old cartesian system custom firmware had some acceleration issues. May be this new polar kinematics in Marlin would fix your issue.

If you already using the marlin firmware with polar kinematics, Then I am not exactly sure what it would be. I tested it for almost  hundred prints and I don't see acceleration problem.
May be the DEFAULT_SEGMENTS_PER_SECOND  in the configuration.h would create such problem. You can try reducing it.

POLAR_FAST_RADIUS in the configuration.h designed to overcome 3D printing extrusion problems and weird feedrates on the center of the polar axis. If you have any movement inside this radius circle, it uses maximum speed that your configuration allows. You can try to reduce it and see if it helps. These all very related to your hardware setup.  So I don't think I can replicate the problem without your exact hardware.

About this video:
https://youtube.com/shorts/HvbnYGIs35s?feature=share

I believe the result should be a straight line. If so, You have a significant offset on the tool. Which means, your tooltip is not aligned to the center of the polar axis. Therefore there is an offset and there is an unreachable radius on the center.

You have two options :
1 - Move the tooltip to exact center of the polar axis mechanically.
2 - Measure the offset and enter it as POLAR_CENTER_OFFSET on the configuration.h file in the Marlin. This option will leave an unreachable circle and crop everything in this circle.

For the Z axis problem;
Polar axis calculations has nothing to do with Z axis. I don't think it would be related to the polar kinematics. I have two different machine with different boards. I didn't observe any problem with Z.

I would suggest you to make sure;
-  There is no torque problem on your Z setup. It can cause only down direction. If the motor just have enough torque to move the Z axis up, it can reduce by time because of heat ( both on the driver or the motor ).
- Z acceleration is low enough to handle the Z axis weight.
- There is no electrical noise on end stops etc.

Rob's firmware uses scara kinematics to achieve polar movements. If any of the firmware won't completely fix the Z problem, It feels like it is more likely a torque or acceleration thing.

If you can share more details ( pictures may be ) about your hardware, it would help me to understand.

Melkiyby, 2023-02-01:
Thanks for the quick response.  The first request is to take a video of how the rotation of the table behaves in your case.  X Axis and Y Axis are programmatically set to zero and send the x axis to -1mm.  A little clarification, I don't use homing at the moment.  Maybe it affects the firmware.
At the moment I'm using the latest (yesterday's) 2.1.x bugfix and the edited config from your post.  Hardware BTT Skr pro and tmc2209 with uart.  In my config, backlash compensation is activated for two linear axes.  S-curve and adaptive step smoothing are disabled.  I tried to activate linear advance - the result is the same.

kadirilkimen, 2023-02-01:
If your machine is not a babyBear, it is probably better to move this conversation to the Marlin firmware repository.

I will perform some tests when I have time of course. And actually made very similar tests in different dimensions. In my case, I didnt notice skipping steps.

I have this video right now: https://youtube.com/shorts/hO4HH4sqpeg?feature=share

It periodicly draws lines passing from zero and cause 180degree rotation. As you can see, there is no any shift on the print. There are more aggressive prints, I am going to upload a video about the babyBear.

Anyway, Since polar coordinates are not offsetting friendly like cartesians, setting zero point for X axis programmatically is a bad idea.

I strongly suggest to install an end switch to locate zero point of X axis on the exact center of the rotary axis.

Your machine's design is also important. What is the reduction ratio of the polar axis?

If you have a small reduction like 3:1 and if you perform a very small movement near center with a slow feedrate,  it may be the reason of the vibration.

Please, if your machine is not a babyBear, open an issue for marlin firmware and I will continue there. If the machine is a babyBear, lets keep the conversation here.

Please provide the following details:

- Share the structure of your machine.

- Share the both configuration file. So we can see if something off.

Melkiyby, 2023-02-02:
Hi. I have posted my issue in the marlin repository [https://github.com/MarlinFirmware/Marlin/issues/25330](url)

kadirilkimen, 2023-02-03:
Anyone experiences this problem, please follow the issue opened in Marlin repository : https://github.com/MarlinFirmware/Marlin/issues/25330

Closed 2023-02-03.

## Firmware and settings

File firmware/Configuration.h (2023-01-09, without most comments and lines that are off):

#pragma once
#define CONFIGURATION_H_VERSION 02010200
#define STRING_CONFIG_H_AUTHOR "kadir ilkimen" // Who made the changes.
#define SHOW_BOOTSCREEN
  #define MOTHERBOARD BOARD_MKS_ROBIN_NANO_V3_1
#define SERIAL_PORT -1
#define BAUDRATE 115200
#define CUSTOM_MACHINE_NAME "babyBear"
#define MACHINE_UUID "05f289b7-ec54-4326-826a-2b942453ea2a"
#define X_DRIVER_TYPE  TMC2209
#define Y_DRIVER_TYPE  TMC2209
#define Z_DRIVER_TYPE  TMC2209
#define E0_DRIVER_TYPE TMC2209
#define EXTRUDERS 1
#define DEFAULT_NOMINAL_FILAMENT_DIA 1.75
#define TEMP_SENSOR_0 5
#define TEMP_SENSOR_1 0
#define TEMP_SENSOR_2 0
#define TEMP_SENSOR_3 0
#define TEMP_SENSOR_4 0
#define TEMP_SENSOR_5 0
#define TEMP_SENSOR_6 0
#define TEMP_SENSOR_7 0
#define TEMP_SENSOR_BED 0
#define TEMP_SENSOR_PROBE 0
#define TEMP_SENSOR_CHAMBER 0
#define TEMP_SENSOR_COOLER 0
#define TEMP_SENSOR_BOARD 0
#define TEMP_SENSOR_REDUNDANT 0
#define DUMMY_THERMISTOR_998_VALUE  25
#define DUMMY_THERMISTOR_999_VALUE 100
#if TEMP_SENSOR_IS_MAX_TC(0)
  #define MAX31865_SENSOR_OHMS_0      100 // (Ω) Typically 100 or 1000 (PT100 or PT1000)
  #define MAX31865_CALIBRATION_OHMS_0 430 // (Ω) Typically 430 for Adafruit PT100; 4300 for Adafruit PT1000
#endif
#if TEMP_SENSOR_IS_MAX_TC(1)
  #define MAX31865_SENSOR_OHMS_1      100
  #define MAX31865_CALIBRATION_OHMS_1 430
#endif
#if TEMP_SENSOR_IS_MAX_TC(2)
  #define MAX31865_SENSOR_OHMS_2      100
  #define MAX31865_CALIBRATION_OHMS_2 430
#endif
#if HAS_E_TEMP_SENSOR
  #define TEMP_RESIDENCY_TIME         10  // (seconds) Time to wait for hotend to "settle" in M109
  #define TEMP_WINDOW                  1  // (°C) Temperature proximity for the "temperature reached" timer
  #define TEMP_HYSTERESIS              3  // (°C) Temperature proximity considered "close enough" to the target
#endif
#if TEMP_SENSOR_BED
  #define TEMP_BED_RESIDENCY_TIME     10  // (seconds) Time to wait for bed to "settle" in M190
  #define TEMP_BED_WINDOW              1  // (°C) Temperature proximity for the "temperature reached" timer
  #define TEMP_BED_HYSTERESIS          3  // (°C) Temperature proximity considered "close enough" to the target
#endif
#if TEMP_SENSOR_CHAMBER
  #define TEMP_CHAMBER_RESIDENCY_TIME 10  // (seconds) Time to wait for chamber to "settle" in M191
  #define TEMP_CHAMBER_WINDOW          1  // (°C) Temperature proximity for the "temperature reached" timer
  #define TEMP_CHAMBER_HYSTERESIS      3  // (°C) Temperature proximity considered "close enough" to the target
#endif
#if TEMP_SENSOR_REDUNDANT
  #define TEMP_SENSOR_REDUNDANT_SOURCE    E1  // The sensor that will provide the redundant reading.
  #define TEMP_SENSOR_REDUNDANT_TARGET    E0  // The sensor that we are providing a redundant reading for.
  #define TEMP_SENSOR_REDUNDANT_MAX_DIFF  10  // (°C) Temperature difference that will trigger a print abort.
#endif
#define HEATER_0_MINTEMP   5
#define HEATER_1_MINTEMP   5
#define HEATER_2_MINTEMP   5
#define HEATER_3_MINTEMP   5
#define HEATER_4_MINTEMP   5
#define HEATER_5_MINTEMP   5
#define HEATER_6_MINTEMP   5
#define HEATER_7_MINTEMP   5
#define BED_MINTEMP        5
#define CHAMBER_MINTEMP    5
#define HEATER_0_MAXTEMP 275
#define HEATER_1_MAXTEMP 275
#define HEATER_2_MAXTEMP 275
#define HEATER_3_MAXTEMP 275
#define HEATER_4_MAXTEMP 275
#define HEATER_5_MAXTEMP 275
#define HEATER_6_MAXTEMP 275
#define HEATER_7_MAXTEMP 275
#define BED_MAXTEMP      150
#define CHAMBER_MAXTEMP  60
#define HOTEND_OVERSHOOT 15   // (°C) Forbid temperatures over MAXTEMP - OVERSHOOT
#define BED_OVERSHOOT    10   // (°C) Forbid temperatures over MAXTEMP - OVERSHOOT
#define COOLER_OVERSHOOT  2   // (°C) Forbid temperatures closer than OVERSHOOT
#define PIDTEMP          // See the PID Tuning Guide at https://reprap.org/wiki/PID_Tuning
#define BANG_MAX 255     // Limits current to nozzle while in bang-bang mode; 255=full current
#define PID_MAX BANG_MAX // Limits current to nozzle while PID is active (see PID_FUNCTIONAL_RANGE below); 255=full current
#define PID_K1 0.95      // Smoothing factor within any PID loop
    #define DEFAULT_Kp  22.20
    #define DEFAULT_Ki   1.08
    #define DEFAULT_Kd 114.00
#define MAX_BED_POWER 255 // limits duty cycle to bed; 255=full current
#define MAX_CHAMBER_POWER 255 // limits duty cycle to chamber heater; 255=full current
  #define PID_FUNCTIONAL_RANGE 10 // If the temperature difference between the target temperature and the actual temperature
#define PREVENT_COLD_EXTRUSION
#define EXTRUDE_MINTEMP 170
#define PREVENT_LENGTHY_EXTRUDE
#define EXTRUDE_MAXLENGTH 200
#define THERMAL_PROTECTION_HOTENDS // Enable thermal protection for all extruders
#define THERMAL_PROTECTION_BED     // Enable thermal protection for the heated bed
#define THERMAL_PROTECTION_CHAMBER // Enable thermal protection for the heated chamber
#define THERMAL_PROTECTION_COOLER  // Enable thermal protection for the laser cooling
#define POLAR
  #define DEFAULT_SEGMENTS_PER_SECOND 180
  #define POLAR_PRINTABLE_RADIUS 82.0f
  #define POLAR_FAST_RADIUS 3.0f
  #define POLAR_CENTER_OFFSET 0.0f
  #define POLAR_FEEDRATE_SCALING  // Convert XY feedrate from mm/s to degrees/s on the fly
#define USE_XMIN_PLUG
#define USE_YMIN_PLUG
#define USE_ZMIN_PLUG
#define ENDSTOPPULLUPS
#define X_MIN_ENDSTOP_INVERTING true // Set to true to invert the logic of the endstop.
#define Y_MIN_ENDSTOP_INVERTING false // Set to true to invert the logic of the endstop.
#define Z_MIN_ENDSTOP_INVERTING true // Set to true to invert the logic of the endstop.
#define I_MIN_ENDSTOP_INVERTING false // Set to true to invert the logic of the endstop.
#define J_MIN_ENDSTOP_INVERTING false // Set to true to invert the logic of the endstop.
#define K_MIN_ENDSTOP_INVERTING false // Set to true to invert the logic of the endstop.
#define U_MIN_ENDSTOP_INVERTING false // Set to true to invert the logic of the endstop.
#define V_MIN_ENDSTOP_INVERTING false // Set to true to invert the logic of the endstop.
#define W_MIN_ENDSTOP_INVERTING false // Set to true to invert the logic of the endstop.
#define X_MAX_ENDSTOP_INVERTING false // Set to true to invert the logic of the endstop.
#define Y_MAX_ENDSTOP_INVERTING false // Set to true to invert the logic of the endstop.
#define Z_MAX_ENDSTOP_INVERTING false // Set to true to invert the logic of the endstop.
#define I_MAX_ENDSTOP_INVERTING false // Set to true to invert the logic of the endstop.
#define J_MAX_ENDSTOP_INVERTING false // Set to true to invert the logic of the endstop.
#define K_MAX_ENDSTOP_INVERTING false // Set to true to invert the logic of the endstop.
#define U_MAX_ENDSTOP_INVERTING false // Set to true to invert the logic of the endstop.
#define V_MAX_ENDSTOP_INVERTING false // Set to true to invert the logic of the endstop.
#define W_MAX_ENDSTOP_INVERTING false // Set to true to invert the logic of the endstop.
#define Z_MIN_PROBE_ENDSTOP_INVERTING false // Set to true to invert the logic of the probe.
#define ENDSTOP_INTERRUPTS_FEATURE
#define DEFAULT_AXIS_STEPS_PER_UNIT   { 100, 66.66666666666667, 200, 415 }
#define DEFAULT_MAX_FEEDRATE          { 400, 350, 100, 50 }
#define DEFAULT_MAX_ACCELERATION      { 2000, 1500, 500, 10000 }
#define DEFAULT_ACCELERATION          2000    // X, Y, Z and E acceleration for printing moves
#define DEFAULT_RETRACT_ACCELERATION  2000    // E acceleration for retracts
#define DEFAULT_TRAVEL_ACCELERATION   2000    // X, Y, Z acceleration for travel (non printing) moves
#define CLASSIC_JERK
  #define DEFAULT_XJERK 10.0
  #define DEFAULT_YJERK 10.0
  #define DEFAULT_ZJERK  2.0
#define DEFAULT_EJERK    10.0  // May be used by Linear Advance
#define Z_MIN_PROBE_USES_Z_MIN_ENDSTOP_PIN
#define NOZZLE_TO_PROBE_OFFSET { 10, 10, 0 }
#define PROBING_MARGIN 10
#define XY_PROBE_FEEDRATE (133*60)
#define Z_PROBE_FEEDRATE_FAST (4*60)
#define Z_PROBE_FEEDRATE_SLOW (Z_PROBE_FEEDRATE_FAST / 2)
#define Z_CLEARANCE_DEPLOY_PROBE   10 // Z Clearance for Deploy/Stow
#define Z_CLEARANCE_BETWEEN_PROBES  5 // Z Clearance between probe points
#define Z_CLEARANCE_MULTI_PROBE     5 // Z Clearance between multiple probes
#define Z_PROBE_LOW_POINT          -2 // Farthest distance below the trigger-point to go before stopping
#define Z_PROBE_OFFSET_RANGE_MIN -20
#define Z_PROBE_OFFSET_RANGE_MAX 20
#define X_ENABLE_ON 0
#define Y_ENABLE_ON 0
#define Z_ENABLE_ON 0
#define E_ENABLE_ON 0 // For all extruders
#define DISABLE_X false
#define DISABLE_Y false
#define DISABLE_Z false
#define DISABLE_E false             // Disable the extruder when not stepping
#define DISABLE_INACTIVE_EXTRUDER   // Keep only the active extruder enabled
#define INVERT_X_DIR true
#define INVERT_Y_DIR false
#define INVERT_Z_DIR true
#define INVERT_E0_DIR true
#define INVERT_E1_DIR false
#define INVERT_E2_DIR false
#define INVERT_E3_DIR false
#define INVERT_E4_DIR false
#define INVERT_E5_DIR false
#define INVERT_E6_DIR false
#define INVERT_E7_DIR false
#define X_HOME_DIR -1
#define Y_HOME_DIR -1
#define Z_HOME_DIR -1
#define X_BED_SIZE 164.0
#define Y_BED_SIZE 164.0
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

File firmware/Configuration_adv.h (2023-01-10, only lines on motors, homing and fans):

#define E0_AUTO_FAN_PIN -1
#define E1_AUTO_FAN_PIN -1
#define E2_AUTO_FAN_PIN -1
#define E3_AUTO_FAN_PIN -1
#define E4_AUTO_FAN_PIN -1
#define E5_AUTO_FAN_PIN -1
#define E6_AUTO_FAN_PIN -1
#define E7_AUTO_FAN_PIN -1
#define CHAMBER_AUTO_FAN_PIN -1
#define COOLER_AUTO_FAN_PIN -1
#define HOMING_BUMP_MM      { 5, 5, 5 }         // (linear=mm, rotational=°) Backoff from endstops after first bump
#define HOMING_BUMP_DIVISOR { 2, 2, 2 }       // Re-Bump Speed Divisor (Divides the Homing Feedrate)
#define MICROSTEP_MODES { 16, 16, 16, 16, 16, 16 } // [1,2,4,8,16]
#define LIN_ADVANCE
    #define ADVANCE_K 0.15        // (mm) Compression length applying to all extruders
  #define ADVANCE_K_EXTRA       // Add a second linear advance constant, configurable with M900 L.
#define ADVANCED_OK
    #define X_CURRENT       1000        // (mA) RMS current. Multiply by 1.414 for peak current.
    #define X_CURRENT_HOME  X_CURRENT  // (mA) RMS current for sensorless homing
    #define X_MICROSTEPS     16        // 0..256
    #define Y_CURRENT       1000
    #define Y_CURRENT_HOME  Y_CURRENT
    #define Y_MICROSTEPS     16
    #define Z_CURRENT       1000
    #define Z_CURRENT_HOME  Z_CURRENT
    #define Z_MICROSTEPS     8
    #define E0_CURRENT      1000
    #define E0_MICROSTEPS    16
  #define HYBRID_THRESHOLD
  #define X_HYBRID_THRESHOLD     100  // [mm/s]
  #define X2_HYBRID_THRESHOLD    100
  #define Y_HYBRID_THRESHOLD     100
  #define Y2_HYBRID_THRESHOLD    100
  #define Z_HYBRID_THRESHOLD       3
  #define Z2_HYBRID_THRESHOLD      3
  #define Z3_HYBRID_THRESHOLD      3
  #define Z4_HYBRID_THRESHOLD      3
  #define I_HYBRID_THRESHOLD       3  // [linear=mm/s, rotational=°/s]
  #define J_HYBRID_THRESHOLD       3  // [linear=mm/s, rotational=°/s]
  #define K_HYBRID_THRESHOLD       3  // [linear=mm/s, rotational=°/s]
  #define U_HYBRID_THRESHOLD       3  // [mm/s]
  #define V_HYBRID_THRESHOLD       3
  #define W_HYBRID_THRESHOLD       3
  #define E0_HYBRID_THRESHOLD     30
  #define E1_HYBRID_THRESHOLD     30
  #define E2_HYBRID_THRESHOLD     30
  #define E3_HYBRID_THRESHOLD     30
  #define E4_HYBRID_THRESHOLD     30
  #define E5_HYBRID_THRESHOLD     30
  #define E6_HYBRID_THRESHOLD     30
  #define E7_HYBRID_THRESHOLD     30
    #define TMC_HOME_PHASE { 640, 640, 640 }

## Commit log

2022-12-01 3D models of the babyBear
    [Bearing-cover.stl, Bottom-cover.stl, Cable-channel.stl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]
2022-12-04 BOM update
    [Components.ods, Fastener.ods, Tools.ods]
2022-12-05 Some other initial updates
    [Components.ods, Tools.ods]
2022-12-05 BOM updates
    [Components.ods, Fastener.ods, acrylic-workbed-surface.dwg]
2022-12-06 Consumables update
    [Components.ods, Consumables.ods, Fastener.ods]
2022-12-06 Suggested color updates and name fixes
    [Rotary-axis-bearing-lock-nut.stl, Rotary-axis-preload-nut.stl, Rotary-axis-rotor-nut.stl]
2022-12-10 Design updates
    [Main-body.stl]
2022-12-16 babyBear Firmware configuration
    [Configuration.h, Configuration_adv.h, esp32.csv]
2022-12-17 Firmware adjustments
    [Configuration.h, Configuration_adv.h]
2022-12-18 3D and BOM update
    [Bottom-cover.stl, Cable-channel.stl, Components.ods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]
2022-12-18 Cura profile update for the babyBear
    [the+babyBear.global.cfg]
2022-12-19 Printing recommendations update
2022-12-20 GT2 Pulley print suggestion updates
2022-12-21 Extruder update
    [Components.ods, Configuration.h, Configuration_adv.h]
2022-12-22 Extruder parameters update
    [Configuration.h, Configuration_adv.h, Hotend-calibration-lines.stl]
2023-01-09 Firmware based Polar Kinematics added
    Marlin now has polar kinematics.
    [Configuration.h, Configuration_adv.h]
2023-01-09 Firmware kinematics update information
2023-01-10 Information update
    [Configuration_adv.h]
2023-01-11 Firmware update
    [Configuration.h, Configuration_adv.h, esp32.csv]
2023-01-15 repository fix
    [Configuration.h, Configuration_adv.h]
2023-02-18 Fixed broken assembly animation link

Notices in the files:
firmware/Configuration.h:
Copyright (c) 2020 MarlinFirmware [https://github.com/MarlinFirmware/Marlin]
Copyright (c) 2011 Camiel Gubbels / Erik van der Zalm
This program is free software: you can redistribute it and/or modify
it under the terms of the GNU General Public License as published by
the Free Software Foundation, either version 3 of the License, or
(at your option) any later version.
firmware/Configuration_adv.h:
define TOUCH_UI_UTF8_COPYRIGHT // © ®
